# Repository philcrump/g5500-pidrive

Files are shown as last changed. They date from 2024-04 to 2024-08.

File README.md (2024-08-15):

# G-5500 PiDrive

***This project is a work in progress, very little testing has so far been done, I supply no guarantee that the basic concepts work***

Controlling an AC-type Yaesu G-5500 Az+El Rotator with PWM from a Raspberry Pi, allowing a portable and compact drive unit running off a 12V battery with no mains inverters.

Choices have been made to use high-end voltage-isolated parts to allow easy co-existence with multiple power domains, as several RF receivers will also be connected to the Raspberry Pi.

## Physical Form Factor

PWM board intends to mount on the _back_ of an RPI DIN Plate, facing the Host Raspberry Pi on another DIN plate, connected by Adafruit GPIO Ribbon Cable.
* https://thepihut.com/products/dinrplate-2-raspberry-pi-din-rail-mount

PCB Render:

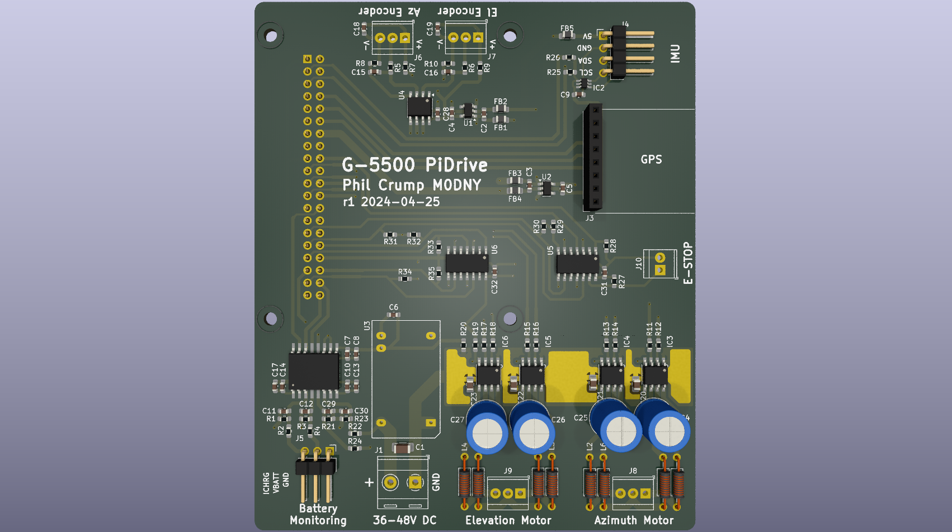
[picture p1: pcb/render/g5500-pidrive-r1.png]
PCB CAD Render


### Supply Voltage

36-48V Input, Tracpower Isolated TEL 12-4811WI DC-DC converts down to 5.1V @ 2.4A for the Raspberry Pi.

MAX22530 12-bit Isolated ADC cam measure the input voltage, and also exposes a connector to measure 12V battery voltage, and an optional extra channel (charge current?)

## G-5500 Control

### Motor Drive

Yaesu mains control box produces 80V pk-pk AC. Initially I plan to use a cheap 12V -> 36V DC-DC step-up to allow output of 72V pk-pk AC. The design allows for increasing to 48V motor bus voltage.

DRV8251A 4.1A Motor drivers used to achieve 50Hz AC PWM over the relevant winding for each direction. Initial experiments with variable-frequency were not very successful, but there may be +/-10% to play with for accel/decel softening.

E-STOP implemented with hardware logic (high-speed CMOS) holds motors in 'Brake' regardless of software - if switch contact is opened.

Footprints have been included to allow the use of RF chokes on the PWM outputs if RFI problems are encountered.

### Potentiometer sensing

MCP3202 12-bit ADC measures the wiper voltage on each of the Az+El Potentiometers to sense position. Careful decoupling of the supply voltage and filtering of the wiper voltage is implemented to achieve a low-noise result.

## Position / Alignment Sensors

* Uputronics Ublox GPS Breakout as daughterboard for Time + Position https://store.uputronics.com/index.php?route=product/product&path=64&product_id=84
* * Connection for NTPD Timing setup with PPS https://austinsnerdythings.com/2021/04/19/microsecond-accurate-ntp-with-a-raspberry-pi-and-pps-gps/

* BNO055 DOF IMU Fusion for magnetic-north calibration https://thepihut.com/products/adafruit-9-dof-absolute-orientation-imu-fusion-breakout-bno055
* * Mounted at end of aluminium boom
* * Active I2C LTC4311 Terminator to extend the I2C far enough down the boom (screened cable will be used.)

## Software

Motor drive using pigpio's excellent ability to run hardware-timed PWM on every GPIO. https://abyz.me.uk/rpi/pigpio/index.html

## Tests

* Body diode clamping of high-z driver on other pole is enough to prevent motion of AC motor.
* Heatsinking of existing drivers is very inadequate. (Blown EL_B1/EL_B2 )
* * Added DIY copper tab heatsinks to both side of PCB
* 22R resistor between 48V & 5V ground domains had approx 1V across it (~50mA)
* * Removed & shorted out.

* Pi Running: 0.07A @ 48V
* 1x Motor drive: 0.67A @ 48V

For attachment to mast pole: https://www.ebay.co.uk/itm/265428394116

ebay wire is 16awg 1.5mm^2

12-48V: https://uk.rs-online.com/web/p/dc-dc-converters/1757784

M3.5 ring terminals for meanwell 12v mains PSU   https://uk.rs-online.com/web/p/ring-terminals/0534222

## Authors

* Phil Crump M0DNY <phil@philcrump.co.uk>

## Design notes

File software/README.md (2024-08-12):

Raspberry Pi OS Bookworm

## C

gcc -Wall -pthread -o pwmtest main.c -lpigpio

# IMU Setup

Raspi-config -> Interface Options ->**Disable** I2C Kernel module.

```bash
sudo bash -c "echo 'dtoverlay=i2c-gpio,i2c_gpio_sda=2,i2c_gpio_scl=3,bus=3' >> /boot/firmware/config.txt"
```
# GPS Setup

Raspi-config -> Interface Options -> Disable Serial Port Console, Enable Serial Port.

( /dev/ttyS0 )

```bash
sudo apt install gpsd pps-tools chrony libgps-dev

sudo bash -c "echo 'dtoverlay=pps-gpio,gpiopin=18' >> /boot/firmware/config.txt"
sudo bash -c "echo 'enable_uart=1' >> /boot/firmware/config.txt"
sudo bash -c "echo 'init_uart_baud=9600' >> /boot/firmware/config.txt"
sudo bash -c "echo 'pps-gpio' >> /etc/modules"
```
Reboot.

Check PPS: `sudo ppstest /dev/pps0`

`sudo nano /etc/default/gpsd`
```
START_DAEMON="true"
USBAUTO="false"
DEVICES="/dev/ttyS0 /dev/pps0"
GPSD_OPTIONS="-n"
```

`sudo systemctl start gpsd`

sudo nano /etc/chrony/chrony.conf

Under pool entry, add:
```
refclock SHM 0 refid NMEA offset 0.000 precision 1e-3 poll 3 noselect
refclock PPS /dev/pps0 refid PPS lock NMEA poll 3
```
sudo systemctl restart chrony

watch -n 1 chronyc sources

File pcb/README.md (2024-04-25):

1x LTC4311 SOT-323-5

4x DRV8251A

4x 8X11.5mm LS:5mm   82uF 63V     667-EEU-FR1J820B 

Ferrites:
0805 40mohm 3A     652-MH2029-800Y

1x 579-MCP3202BISN MCP3202 B-grade SOIC

1x MAX22530AWE+ Isolated ADC

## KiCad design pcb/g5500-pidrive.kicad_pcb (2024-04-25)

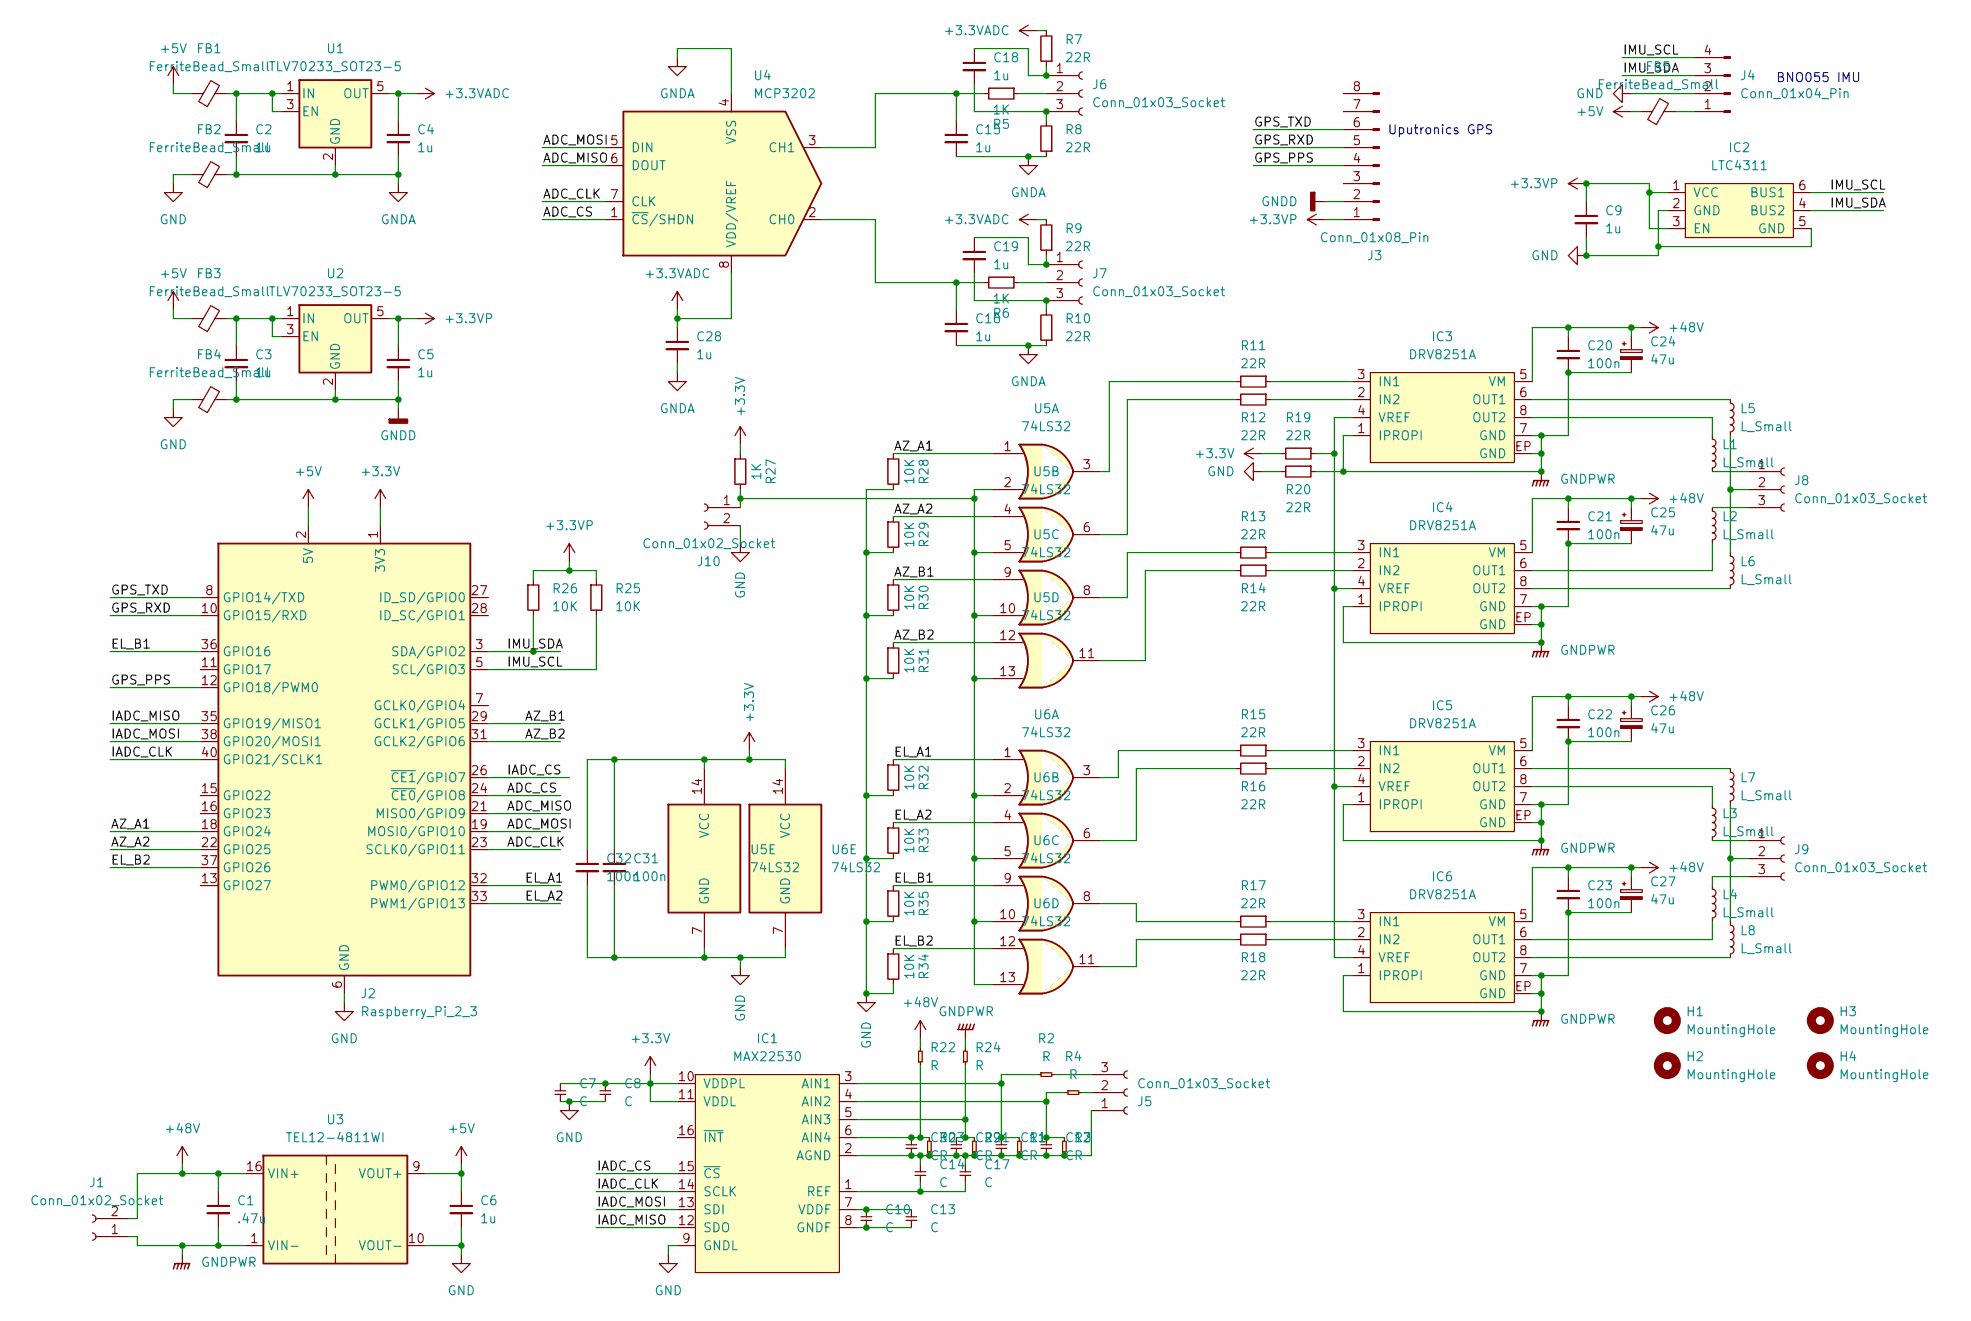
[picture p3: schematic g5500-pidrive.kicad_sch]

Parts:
C1: .47u; C_1206_3216Metric_Pad1.33x1.80mm_HandSolder
C2, C3, C4, C5, C6, C9, C15, C16, C18, C19, C28: 1u; C_0603_1608Metric_Pad1.08x0.95mm_HandSolder
C7, C8, C10, C11, C12, C13, C14, C17, C29, C30: C; C_0603_1608Metric_Pad1.08x0.95mm_HandSolder
C20, C21, C22, C23: 100n; C_0805_2012Metric_Pad1.18x1.45mm_HandSolder
C24, C25, C26, C27: 47u; C_Radial_D8.0mm_H11.5mm_P3.50mm
C31, C32: 100n; C_0603_1608Metric_Pad1.08x0.95mm_HandSolder
FB1, FB2, FB3, FB4, FB5: FerriteBead_Small; L_0805_2012Metric_Pad1.05x1.20mm_HandSolder
H1, H2, H3, H4: MountingHole; MountingHole_2.7mm_M2.5
IC1: MAX22530; SOIC-16-W; Mouser 700-MAX22530AWE+
IC2: LTC4311; SC-70-6; Mouser 584-C4311CSC6TRMPBF
IC3, IC4, IC5, IC6: DRV8251A; SOIC-8-EP; Mouser 595-DRV8251ADDAR
J1: Conn_01x02_Socket; TerminalBlock_RND_205-00287_1x02_P5.08mm_Horizontal
J2: Raspberry_Pi_2_3; PinSocket_2x20_P2.54mm_Vertical
J3: Conn_01x08_Pin; PinSocket_1x08_P2.54mm_Vertical
J4: Conn_01x04_Pin; PinHeader_1x04_P2.54mm_Horizontal
J5: Conn_01x03_Socket; PinHeader_1x03_P2.54mm_Horizontal
J6, J7, J8, J9: Conn_01x03_Socket; TerminalBlock_TE_282834-3_1x03_P2.54mm_Horizontal
J10: Conn_01x02_Socket; TerminalBlock_TE_282834-2_1x02_P2.54mm_Horizontal
L1, L2, L3, L4, L5, L6, L7, L8: L_Small; L_Axial_L5.3mm_D2.2mm_P10.16mm_Horizontal_Vishay_IM-1
R1, R2, R3, R4, R21, R22, R23, R24: R; R_0603_1608Metric_Pad0.98x0.95mm_HandSolder
R5, R6, R27: 1K; R_0603_1608Metric_Pad0.98x0.95mm_HandSolder
R7, R8, R9, R10, R11, R12, R13, R14, R15, R16, R17, R18, R19, R20: 22R; R_0603_1608Metric_Pad0.98x0.95mm_HandSolder
R25, R26, R28, R29, R30, R31, R32, R33, R34, R35: 10K; R_0603_1608Metric_Pad0.98x0.95mm_HandSolder
U1, U2: TLV70233_SOT23-5; SOT-23-5
U3: TEL12-4811WI; Converter_DCDC_TRACO_TEL12-xxxx_THT
U4: MCP3202; SOIC-8_3.9x4.9mm_P1.27mm
U5, U6: 74LS32; SOIC-14

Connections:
+3.3V: C7.2, C8.2, C31.1, C32.1, IC1.10 (VDDPL), IC1.11 (VDDL), J2.1 (3V3), J2.17 (3V3), R19.2, R27.1, U5.14 (VCC), U6.14 (VCC)
+3.3VADC: C4.1, C28.1, R7.2, R9.2, U1.5 (OUT), U4.8 (VDD/VREF)
+3.3VP: C5.1, C9.1, IC2.1 (VCC), IC2.3 (EN), J3.1, R25.1, R26.1, U2.5 (OUT)
+5V: C6.1, FB1.1, FB3.1, FB5.1, J2.2 (5V), J2.4 (5V), U3.9 (VOUT+)
+48V: C1.1, C20.1, C21.1, C22.1, C23.1, C24.1, C25.1, C26.1, C27.1, IC3.5 (VM), IC4.5 (VM), IC5.5 (VM), IC6.5 (VM), J1.2, R22.2, U3.16 (VIN+)
/ADC_CLK: J2.23 (SCLK0/GPIO11), U4.7 (CLK)
/ADC_CS: J2.24 (~CE0/GPIO8), U4.1 (~CS/SHDN)
/ADC_MISO: J2.21 (MISO0/GPIO9), U4.6 (DOUT)
/ADC_MOSI: J2.19 (MOSI0/GPIO10), U4.5 (DIN)
/AZ_A1: J2.18 (GPIO24), R28.1, U5.1
/AZ_A2: J2.22 (GPIO25), R29.1, U5.4
/AZ_B1: J2.29 (GCLK1/GPIO5), R30.1, U5.9
/AZ_B2: J2.31 (GCLK2/GPIO6), R31.1, U5.12
/EL_A1: J2.32 (PWM0/GPIO12), R32.1, U6.1
/EL_A2: J2.33 (PWM1/GPIO13), R33.1, U6.4
/EL_B1: J2.36 (GPIO16), R35.1, U6.9
/EL_B2: J2.37 (GPIO26), R34.1, U6.12
/GPS_PPS: J2.12 (GPIO18/PWM0), J3.4
/GPS_RXD: J2.10 (GPIO15/RXD), J3.5
/GPS_TXD: J2.8 (GPIO14/TXD), J3.6
/IADC_CLK: IC1.14 (SCLK), J2.40 (GPIO21/SCLK1)
/IADC_CS: IC1.15 (~CS), J2.26 (~CE1/GPIO7)
/IADC_MISO: IC1.12 (SDO), J2.35 (GPIO19/MISO1)
/IADC_MOSI: IC1.13 (SDI), J2.38 (GPIO20/MOSI1)
/IMU_SCL: IC2.6 (BUS1), J2.5 (SCL/GPIO3), J4.4, R25.2
/IMU_SDA: IC2.4 (BUS2), J2.3 (SDA/GPIO2), J4.3, R26.2
GND: C6.2, C7.1, C8.1, C9.2, C31.2, C32.2, FB2.1, FB4.1, IC1.9 (GNDL), IC2.2 (GND), IC2.5 (GND), J2.6 (GND), J2.9 (GND), J2.14 (GND), J2.20 (GND), J2.25 (GND), J2.30 (GND), J2.34 (GND), J2.39 (GND), J4.2, J10.2, R20.2, R28.2, R29.2, R30.2, R31.2, R32.2, R33.2, R34.2, R35.2, U3.10 (VOUT-), U5.7 (GND), U6.7 (GND)
GNDA: C2.2, C4.2, C15.2, C16.2, C28.2, FB2.2, R8.1, R10.1, U1.2 (GND), U4.4 (VSS)
GNDD: C3.2, C5.2, FB4.2, J3.2, U2.2 (GND)
GNDPWR: C1.2, C20.2, C21.2, C22.2, C23.2, C24.2, C25.2, C26.2, C27.2, IC3.1 (IPROPI), IC3.7 (GND), IC3.EP (GND), IC4.1 (IPROPI), IC4.7 (GND), IC4.EP (GND), IC5.1 (IPROPI), IC5.7 (GND), IC5.EP (GND), IC6.1 (IPROPI), IC6.7 (GND), IC6.EP (GND), J1.1, R20.1, R24.2, U3.1 (VIN-)
unnamed: C11.1, C12.1, C14.1, C17.1, C29.1, C30.1, IC1.2 (AGND), J5.1, R1.1, R3.1, R21.1, R23.1
unnamed: C11.2, IC1.3 (AIN1), R1.2, R2.1
unnamed: C12.2, IC1.4 (AIN2), R3.2, R4.1
unnamed: C29.2, IC1.5 (AIN3), R21.2, R24.1
unnamed: C30.2, IC1.6 (AIN4), R22.1, R23.2
unnamed: C10.1, C13.1, IC1.8 (GNDF)
unnamed: C14.2, C17.2, IC1.1 (REF)
unnamed: C10.2, C13.2, IC1.7 (VDDF)
unnamed: IC3.3 (IN1), R11.1
unnamed: IC3.2 (IN2), R12.1
unnamed: IC3.6 (OUT1), L5.1
unnamed: IC3.8 (OUT2), L1.1
unnamed: IC3.4 (VREF), IC4.4 (VREF), IC5.4 (VREF), IC6.4 (VREF), R19.1
unnamed: IC4.3 (IN1), R13.1
unnamed: IC4.2 (IN2), R14.1
unnamed: IC4.6 (OUT1), L2.2
unnamed: IC4.8 (OUT2), L6.2
unnamed: IC5.3 (IN1), R15.1
unnamed: IC5.2 (IN2), R16.1
unnamed: IC5.6 (OUT1), L7.1
unnamed: IC5.8 (OUT2), L3.1
unnamed: IC6.3 (IN1), R17.1
unnamed: IC6.2 (IN2), R18.1
unnamed: IC6.6 (OUT1), L4.2
unnamed: IC6.8 (OUT2), L8.2
unnamed: FB5.2, J4.1
unnamed: J5.2, R4.2
unnamed: J5.3, R2.2
unnamed: C18.1, J6.1, R7.1
unnamed: J6.2, R5.1
unnamed: C18.2, J6.3, R8.2
unnamed: C19.1, J7.1, R9.1
unnamed: J7.2, R6.1
unnamed: C19.2, J7.3, R10.2
unnamed: J8.1, L1.2
unnamed: J8.2, L5.2, L6.1
unnamed: J8.3, L2.1
unnamed: J9.1, L3.2
unnamed: J9.2, L7.2, L8.1
unnamed: J9.3, L4.1
unnamed: J10.1, R27.2, U5.2, U5.5, U5.10, U5.13, U6.2, U6.5, U6.10, U6.13
unnamed: R11.2, U5.3
unnamed: R12.2, U5.6
unnamed: R13.2, U5.8
unnamed: R14.2, U5.11
unnamed: R15.2, U6.3
unnamed: R16.2, U6.6
unnamed: R17.2, U6.8
unnamed: R18.2, U6.11
unnamed: C2.1, FB1.2, U1.1 (IN), U1.3 (EN)
unnamed: C3.1, FB3.2, U2.1 (IN), U2.3 (EN)
unnamed: C16.1, R6.2, U4.2 (CH0)
unnamed: C15.1, R5.2, U4.3 (CH1)

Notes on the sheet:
Uputronics GPS
BNO055 IMU

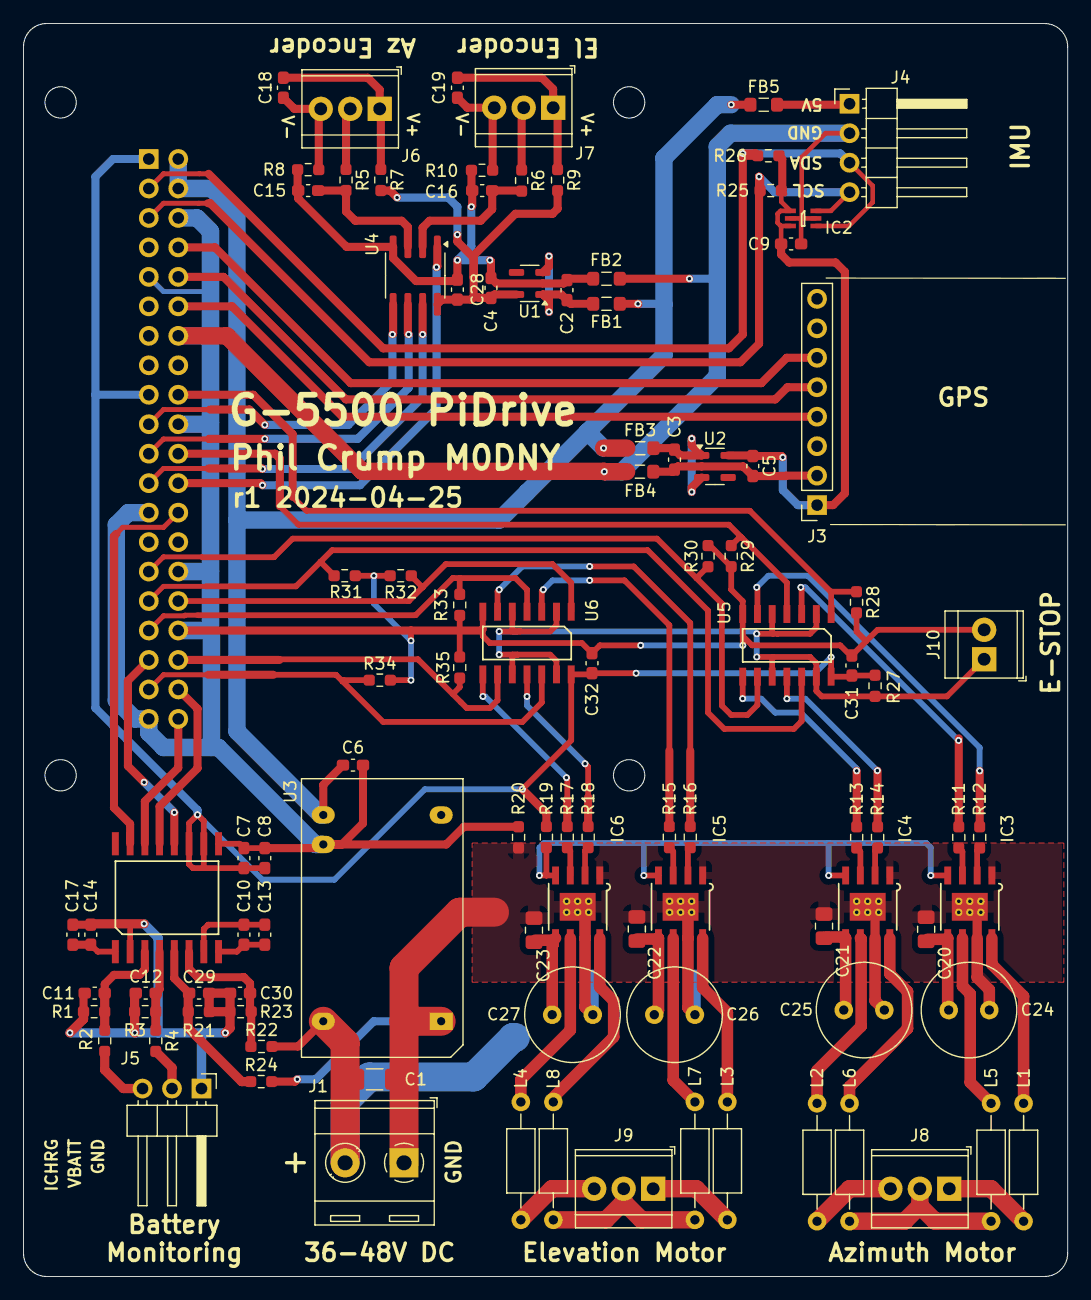
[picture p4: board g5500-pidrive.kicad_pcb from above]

Board: 2 copper layers, 90.0 x 108.0 mm, 106 parts (1 on the bottom side), 83 nets.

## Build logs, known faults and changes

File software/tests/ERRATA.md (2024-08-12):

GPS TX/RX reversed.

MAX ADC SPI CS needs to be connected to GPIO 17.

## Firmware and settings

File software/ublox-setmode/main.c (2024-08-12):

#include <stdio.h>
#include <string.h>
#include <termios.h>
#include <unistd.h>
#include <sys/types.h>
#include <sys/stat.h>
#include <stdint.h>
#include <stdbool.h>
#include <fcntl.h>

bool verbose = false;

const int32_t gnss_aid_position_latitude    = (51.64 / 1e-7); // mid-south-England
const int32_t gnss_aid_position_longitude   = (-1.48 / 1e-7);
const int32_t gnss_aid_position_altitude    =    (10 / 1e-2); // 10m
const int32_t gnss_aid_position_stddev      =   (199 / 1e-5); // 199km

uint8_t gnss_hard_reset[] =
    {   0xB5, 0x62,
        0x06, 0x04, // UBX-CFG-RST
        0x04, 0x00, // Length
        0xff, 0xff, // navBbrMask (0 = hot, 1 = warm, ffff = cold)
        0x04, // resetMode (0 = hardware, 1 = software, 2 = gnss, 4 = shutdown then hardware)
        0x00, // Reserved
        0x00, 0x00 // Checksum
    };

uint8_t gnss_aid_position[] =
    {   0xB5, 0x62,
        0x13, 0x40, // UBX-MGA-INI
        0x14, 0x00, // Length
        0x01, // Type: UBX-MGA-INI-POS_LLH
        0x00, // Version: 0
        0x00, 0x00, // Reserved
        0x00, 0x00, 0x00, 0x00, // Latitude 1e-7
        0x00, 0x00, 0x00, 0x00, // Longitude 1e-7
        0x00, 0x00, 0x00, 0x00, // Altitude cm
        0x00, 0x00, 0x00, 0x00, // Std Dev cm
        0x00, 0x00 // Checksum
    };

uint8_t set_navmodel_stationary[] =
    {   0xB5, 0x62,
        0x06, 0x24, // UBX-CFG-NAV5
        0x24, 0x00, // Length 
        0xFF, 0xFF, // Bitmask
        0x02, // Model (Stationary = 0x02, airborne = 0x06)
        0x03, // Fix Type (Auto 2D/3D)
        0x00, 0x00, 0x00, 0x00, // 2D Altitude Value
        0x10, 0x27, 0x00, 0x00, // 2D Altitude Variance
        0x05, // Minimum GNSS Satellite Elevation
        0x00, // Reserved
        0xFA, 0x00, // Position DOP Mask
        0xFA, 0x00, // Time DOP Mask
        0x64, 0x00, // Position Accuracy Mask
        0x2C, 0x01, // Time Accuracy Mask
        0x00, // Static hold threshold
        0x00, // DGNSS Timeout
        0x00, // Min Satellites for Fix
        0x00, // Min C/N0 Threshold for Satellites
        0x10, 0x27, // Reserved
        0x00, 0x00, // Static Hold Distance Threshold
        0x00, // UTC Standard (Automatic)
        0x00, 0x00, 0x00, 0x00, 0x00,
        0x00, 0x00 // Checksum
    };

uint8_t set_sbas_egnos[] =
    {   0xB5, 0x62,
        0x06, 0x16, // UBX-CFG-SBAS
        0x08, 0x00, // Length
        0x01, // Mode (enabled)
        0x07, // Usage (range, corrections, integrity)
        0x03, // SBAS Channels (3, field obselete)
        0x00, 0x51, 0x08, 0x00, 0x00, // PRN Bitmask (EGNOS-only)
        0x00, 0x00 // Checksum
    };

void usage( void )
{
    printf("Usage: ubloxSetMode -d <device>\n");  
}
 
unsigned char ReadBByteFromSerial(int fd, int *k)
{
    unsigned char tmp;
   
    (*k)++;
     
    if (read(fd, &tmp, 1) > 0)
    {
        // if (tmp & 0x80)
        // {
            // printf("<%2x> ", tmp);
        // }
        // else
        // {
            // printf("%c", tmp);
        // }
    }
   
    return tmp;
}

void calcChecksum(uint8_t *command, int32_t command_length)
{
    uint8_t ck_a = 0, ck_b = 0;
    for(int32_t i = 2; i < (command_length-2); i++)
    {
        ck_a += command[i];
        ck_b += ck_a;
    }
    command[command_length-2] = ck_a;
    command[command_length-1] = ck_b;

    //printf("ck: 0x%02x, 0x%02x\n", ck_a, ck_b);
}

bool setMode(int fd, uint8_t *command, int32_t command_length)
{
    int Retries, k;
    bool result;

    Retries = 0;
    k = 0;
    result = false;
   
    while ((Retries < 5) && !result)
    {
        calcChecksum(command, command_length);

        if(verbose) printf(">> Sending Command (Attempt %d of 5) >>\n", (Retries+1));
        if(write(fd, command, command_length) != command_length)
        {
            Retries++;
            continue;
        }
       
        Retries++;
        k = 0;
       
        if(verbose) printf("<< Receiving ACK <<\n");
        while ((k < 1000) && !result)
        {
            /* Check for ACK */
            if (ReadBByteFromSerial(fd, &k) == 0xb5)
            {
                if (ReadBByteFromSerial(fd, &k) == 0x62)
                {
                    if (ReadBByteFromSerial(fd, &k) == 0x05)
                    {
                        if (ReadBByteFromSerial(fd, &k) == 0x01)
                        {
                            ReadBByteFromSerial(fd, &k);
                            ReadBByteFromSerial(fd, &k);

                            /* Check ACK is for correct message ID */
                            if (ReadBByteFromSerial(fd, &k) == command[2])
                            {
                                if (ReadBByteFromSerial(fd, &k) == command[3])
                                {
                                    if(verbose) printf("|| Received ACK OK!\n");
                                    result = true;
                                }
                            }
                        }
                    }
                }
            }
        }
    }

    return result;
}
 
int main(int argc, char *argv[])
{   
    bool result;
    int fd;
    int option = 0;
    char devName[50];
    struct termios options;
   
    memset(devName, 0, sizeof(devName));
    while((option = getopt( argc, argv, "vd:")) != -1)
    {
        switch(option)
        {
            case 'd':
                printf("Configuring serial device: %s\n", optarg);
                strncpy(devName, optarg, sizeof(devName)-1);                
                break;
            case 'v':
                printf(" * Verbose Mode Enabled\n");
                verbose = true;
                break;
            default:
                usage();
                return 0;
        }        
    }
 
    if(devName[0] == 0)
    {
        usage();
        return 1;
    }
       
    /* Open Serial Port */
    fd = open(devName, O_RDWR);
    if(fd < 0)
    {
        printf("Error: Cannot open serial device '%s'\n", devName);
        return 1;
    }
     
    /* Configure Serial Port */
    tcgetattr(fd, &options);
 
    options.c_lflag &= ~ECHO;
    options.c_cc[VMIN]  = 0;
    options.c_cc[VTIME] = 10;
 
    cfsetispeed(&options, B9600);
    cfsetospeed(&options, B9600);
    options.c_cflag &= ~CSTOPB;
    options.c_cflag &= ~CSIZE;
    options.c_cflag |= CS8;
    options.c_oflag &= ~ONLCR;
    options.c_oflag &= ~OPOST;
    options.c_iflag &= ~IXON;
    options.c_iflag &= ~IXOFF;
 
    tcsetattr(fd, TCSANOW, &options);

    memcpy(&gnss_aid_position[8], &gnss_aid_position_latitude, sizeof(int32_t));
    memcpy(&gnss_aid_position[12], &gnss_aid_position_longitude, sizeof(int32_t));
    memcpy(&gnss_aid_position[16], &gnss_aid_position_altitude, sizeof(int32_t));
    memcpy(&gnss_aid_position[20], &gnss_aid_position_stddev, sizeof(int32_t));
    calcChecksum(gnss_aid_position, sizeof(gnss_aid_position));

    printf("Configuring Position Aid..\n");
    result = setMode(fd, gnss_aid_position, sizeof(gnss_aid_position));
    if(!result)
    {
        printf("** FAILED to configure Position Aid **\n");
        close(fd);
        return 1;
    }

    printf("Configuring Navigation Model..\n");
    result = setMode(fd, set_navmodel_stationary, sizeof(set_navmodel_stationary));
    if(!result)
    {
        printf("** FAILED to configure Navigation Model **\n");
        close(fd);
        return 1;
    }
 
    printf("Configuring SBAS Mode for EGNOS..\n");
    result = setMode(fd, set_sbas_egnos, sizeof(set_sbas_egnos));
    if(!result)
    {
        printf("** FAILED to configure SBAS Mode **\n");
        close(fd);
        return 1;
    }

    close(fd);

    printf("Device Configuration Successful\n");
   
    return 0;
}

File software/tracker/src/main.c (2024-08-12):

#include <stdio.h>
#include <unistd.h>
#include <stdlib.h>
#include <errno.h>
#include <pthread.h>
#include <signal.h>
#include <math.h>

#include <pigpio.h>

#include "main.h"
#include "adc_encoder.h"
#include "adc_supplies.h"
#include "imu.h"
#include "gpsd.h"
#include "motordrive.h"


app_state_t app_state = {
    .demand_valid = false,
    .current_valid = false,
    .voltages_valid = false,
    .gpsd_valid = false,
    .imu_valid = false,
    .compass_valid = false,
    .app_exit = false
};

void sigint_handler(int sig) 
{
    (void)sig;
    printf("\nCTRL-C detected...\n");
    app_state.app_exit = true;
}

int main(int argc, char **argv)
{
    (void)argc;
    (void)argv;

    /* Override pigpio handler */
    signal(SIGINT, sigint_handler);
    signal(SIGTERM, sigint_handler);

    if(gpioInitialise() < 0)
    {
        fprintf(stderr, "Error: gpio failed to initialise\n");
        return 1;
    }
    gpioWaveClear();

    //printf("pigpio version %d.\n", gpioVersion());
    //printf("Hardware revision %d.\n", gpioHardwareRevision());

    /* Override pigpio handler */
    signal(SIGINT, sigint_handler);
    signal(SIGTERM, sigint_handler);

    // threads
    pthread_t adcs_pthread;
    pthread_t imu_obj;
    pthread_t gpsd_obj;
    pthread_t motordrive_obj;

    // ADC Encoders Thread
    if(0 != pthread_create(&adcs_pthread, NULL, adc_loop, (void *)&app_state))
    {
        fprintf(stderr, "Error creating %s pthread\n", "adc_encoder");
        return 1;
    }
    pthread_setname_np(adcs_pthread, "adcs");

    // IMU Thread
    if(0 != pthread_create(&imu_obj, NULL, imu_thread, (void *)&app_state))
    {
        fprintf(stderr, "Error creating %s pthread\n", "imu");
        return 1;
    }
    pthread_setname_np(imu_obj, "imu");

    // GPSD Thread
    if(0 != pthread_create(&gpsd_obj, NULL, gpsd_thread, (void *)&app_state))
    {
        fprintf(stderr, "Error creating %s pthread\n", "gpsd");
        return 1;
    }
    pthread_setname_np(gpsd_obj, "gpsd");

    if(0 != pthread_create(&motordrive_obj, NULL, motordrive_thread, (void *)&app_state))
    {
        fprintf(stderr, "Error creating %s pthread\n", "motordrive");
        return 1;
    }
    pthread_setname_np(motordrive_obj, "motordrive");

    app_state.demand_az_deg = 250.0;
    app_state.demand_el_deg = 90.0;
    app_state.demand_valid = true;


    while(!(app_state.app_exit))
    {
        if(app_state.voltages_valid)
        {
            printf("PoE Voltage: %.2fV, Battery Voltage: %.2fV\n", app_state.poe_voltage, app_state.batt_voltage);
        }
        if(app_state.gpsd_valid)
        {
            if(app_state.gpsd_fixmode >= 2)
            {
                printf("GPS Fix: %dD (%02d), Lat: %.6f, Lon: %.6f\n", app_state.gpsd_fixmode, app_state.gpsd_sats, app_state.gpsd_latitude,  app_state.gpsd_longitude);
            }
            else
            {
                printf("GPS Fix: %dD (%02d)\n", app_state.gpsd_fixmode, app_state.gpsd_sats);
            }
        }
        if(app_state.current_valid)
        {
            printf("Current: Az: %.01f, El: %0.1f\n", app_state.current_az_deg, app_state.current_el_deg);
        }
        if(app_state.imu_valid)
        {
            printf("Heading: %+03.1f (%01x), Roll: %+03.1f, Pitch: %+03.1f\n", app_state.imu_heading, app_state.imu_heading_calstatus, app_state.imu_roll, app_state.imu_pitch);
        }

        usleep(500*1000); // 20 Hz
    }

    printf("Terminating threads..\n");

    pthread_join(adcs_pthread, NULL);
    pthread_join(gpsd_obj, NULL);
    pthread_join(motordrive_obj, NULL);

    printf("Terminating GPIO\n");

    gpioTerminate();

    return 0;
}

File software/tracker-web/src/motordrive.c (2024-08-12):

#include <stdio.h>
#include <stdlib.h>
#include <unistd.h>
#include <stdbool.h>
#include <signal.h>

#include <math.h>
#include <pigpio.h>

#include "main.h"
#include "util/timing.h"

#define AZ_HYSTERESIS   (1.5)
#define EL_HYSTERESIS   (1.0)

#define AZ_RELAY_PAUSE_MS   (200)
#define EL_RELAY_PAUSE_MS   (200)

#define WAVEFORM_POINTS     (1000)
#define WAVEFORM_PERIOD_US  (40)

#define AZ_CW_P     (24)
#define AZ_CW_N     (25)

#define AZ_CCW_P    (5) // unused (popped)
#define AZ_CCW_N    (6) // unused (popped)

#define EL_CW_P     (12)
#define EL_CW_N     (13)

#define EL_CCW_P    (16) //unused
#define EL_CCW_N    (26) // unused

#define AZ_SWITCH_GPIO  (27)
#define EL_SWITCH_GPIO  (22)

void *loop_motordrive(void *arg)
{
  app_state_t *app_state = (app_state_t *)arg;

  float phase_angle, sine_amplitude, duty_cycle;

  gpioPulse_t *az_wf = (gpioPulse_t *)malloc(WAVEFORM_POINTS * sizeof(gpioPulse_t));
  if(az_wf == NULL)
  {
    fprintf(stderr, "Motordrive: Error allocating local memory for waveform\n");
    return NULL;
  }

  gpioPulse_t *el_wf = (gpioPulse_t *)malloc(WAVEFORM_POINTS * sizeof(gpioPulse_t));
  if(el_wf == NULL)
  {
    fprintf(stderr, "Motordrive: Error allocating local memory for waveform\n");
    free(az_wf);
    return NULL;
  }

  gpioPulse_t *azel_wf = (gpioPulse_t *)malloc(WAVEFORM_POINTS * sizeof(gpioPulse_t));
  if(azel_wf == NULL)
  {
    fprintf(stderr, "Motordrive: Error allocating local memory for waveform\n");
    free(az_wf);
    free(el_wf);
    return NULL;
  }

  int gpio_az, gpio_el;

  for(int i = 0; i < WAVEFORM_POINTS; i++)
  {
    phase_angle = i * ((2*M_PI) / (float)WAVEFORM_POINTS);
    sine_amplitude = sin(phase_angle);

    if(sine_amplitude >= 0)
    {
      /* Positive half of wave */
      gpio_az = 1 << (AZ_CW_P);
      gpio_el = 1 << (EL_CW_P);
    }
    else
    {
      gpio_az = 1 << (AZ_CW_N);
      gpio_el = 1 << (EL_CW_N);
    }

    duty_cycle = fabs(sine_amplitude) * 0.9;

    if((i & 0x01) == 0x00)
    {
      az_wf[i].gpioOn = gpio_az;
      el_wf[i].gpioOn = gpio_el;
      azel_wf[i].gpioOn = (gpio_az | gpio_el);

      az_wf[i].gpioOff = 0;
      el_wf[i].gpioOff = 0;
      azel_wf[i].gpioOff = 0;

      az_wf[i].usDelay = (int)(round(duty_cycle * WAVEFORM_PERIOD_US));
      el_wf[i].usDelay = (int)(round(duty_cycle * WAVEFORM_PERIOD_US));
      azel_wf[i].usDelay = (int)(round(duty_cycle * WAVEFORM_PERIOD_US));
    }
    else
    {

      az_wf[i].gpioOn = 0;
      el_wf[i].gpioOn = 0;
      azel_wf[i].gpioOn = 0;

      az_wf[i].gpioOff = gpio_az;
      el_wf[i].gpioOff = gpio_el;
      azel_wf[i].gpioOff = (gpio_az | gpio_el);

      az_wf[i].usDelay = WAVEFORM_PERIOD_US - (int)(round(duty_cycle * WAVEFORM_PERIOD_US));
      el_wf[i].usDelay = WAVEFORM_PERIOD_US - (int)(round(duty_cycle * WAVEFORM_PERIOD_US));
      azel_wf[i].usDelay = WAVEFORM_PERIOD_US - (int)(round(duty_cycle * WAVEFORM_PERIOD_US));
    }
  }

  int e, az_wave, el_wave, azel_wave;

  e = gpioWaveAddGeneric(WAVEFORM_POINTS, az_wf);
  if(e < 0)
  {
    fprintf(stderr, "Failed to add az_wf Waveform to gpio: %d\n", e);
  }
  az_wave = gpioWaveCreate();
  if(az_wave < 0)
  {
    fprintf(stderr, "Failed to create az_wave Waveform: %d\n", e);
  }

  e = gpioWaveAddGeneric(WAVEFORM_POINTS, el_wf);
  if(e < 0)
  {
    fprintf(stderr, "Failed to add el_wf Waveform to gpio: %d\n", e);
  }
  el_wave = gpioWaveCreate();
  if(el_wave < 0)
  {
    fprintf(stderr, "Failed to create el_wave Waveform: %d\n", e);
  }

  e = gpioWaveAddGeneric(WAVEFORM_POINTS, azel_wf);
  if(e < 0)
  {
    fprintf(stderr, "Failed to add azel_wf Waveform to gpio: %d\n", e);
  }
  azel_wave = gpioWaveCreate();
  if(azel_wave < 0)
  {
    fprintf(stderr, "Failed to create azel_wave Waveform: %d\n", e);
  }

  /* Set up outputs */

  gpioSetMode(AZ_CW_P, PI_OUTPUT);
  gpioSetMode(AZ_CW_N, PI_OUTPUT);

  gpioSetMode(AZ_CCW_P, PI_OUTPUT);
  gpioSetMode(AZ_CCW_N, PI_OUTPUT);

  gpioSetMode(EL_CW_P, PI_OUTPUT);
  gpioSetMode(EL_CW_N, PI_OUTPUT);

  gpioSetMode(EL_CCW_P, PI_OUTPUT);
  gpioSetMode(EL_CCW_N, PI_OUTPUT);

  gpioWrite_Bits_0_31_Clear(
    1 << (EL_CW_P) | 1 << (EL_CW_N) | 1 << (EL_CCW_P) | 1 << (EL_CCW_N)
    | 1 << (AZ_CW_P) | 1 << (AZ_CW_N) | 1 << (AZ_CCW_P) | 1 << (AZ_CCW_N)
  );

  /* Direction Relays */
  gpioSetMode(AZ_SWITCH_GPIO, PI_OUTPUT);
  gpioSetMode(EL_SWITCH_GPIO, PI_OUTPUT);

  gpioWrite(AZ_SWITCH_GPIO, 0);
  gpioWrite(EL_SWITCH_GPIO, 0);

  enum WAVE_STATE {
    WAVE_OFF,
    WAVE_AZ,
    WAVE_EL,
    WAVE_AZEL
  };

  int32_t pwm_state = WAVE_OFF;

  int32_t az_relay_state = 0;
  int32_t el_relay_state = 0;

  uint64_t az_relay_lastswitch = timestamp_ms();
  uint64_t el_relay_lastswitch = timestamp_ms();

  /* Run waves */
  while(!(app_state->app_exit))
  {
    if(app_state->demand_valid
      && app_state->encoder_valid
    )
    {
      app_state->error_az_deg = app_state->encoder_az_deg - app_state->demand_az_deg;
      app_state->error_el_deg = app_state->encoder_el_deg - app_state->demand_el_deg;
      app_state->error_lastupdated_ms = timestamp_ms();
      app_state->error_valid = true;

      // Check Azimuth
      if(app_state->error_az_deg > AZ_HYSTERESIS
        && (az_relay_lastswitch + AZ_RELAY_PAUSE_MS) < timestamp_ms())
      {
        if(az_relay_state == 0)
        {
          gpioWrite(AZ_SWITCH_GPIO, 1);
          az_relay_state = 1;

          az_relay_lastswitch = timestamp_ms();
        }
        else
        {
          if(pwm_state != WAVE_AZ && pwm_state != WAVE_AZEL)
          {
            if(pwm_state == WAVE_EL)
            {
              /* Stop the El-only wave */
              gpioWaveTxStop();
              gpioWrite_Bits_0_31_Clear(
                1 << (EL_CW_P) | 1 << (EL_CW_N) | 1 << (EL_CCW_P) | 1 << (EL_CCW_N)
                | 1 << (AZ_CW_P) | 1 << (AZ_CW_N) | 1 << (AZ_CCW_P) | 1 << (AZ_CCW_N)
              );
              /* Start the az-el wave */
              e = gpioWaveTxSend(azel_wave, PI_WAVE_MODE_REPEAT);
              if(e < 0)
              {
                fprintf(stderr, "Failed to send Az drive waveform: %d\n", e);
              }
              pwm_state = WAVE_AZEL;
            }
            else
            {
              /* Start the az-only wave */
              e = gpioWaveTxSend(az_wave, PI_WAVE_MODE_REPEAT);
              if(e < 0)
              {
                fprintf(stderr, "Failed to send Az drive waveform: %d\n", e);
              }
              pwm_state = WAVE_AZ;
            }
          }
        }
      }
      else if(app_state->error_az_deg < (-1 * AZ_HYSTERESIS)
        && (az_relay_lastswitch + AZ_RELAY_PAUSE_MS) < timestamp_ms())
      {
        if(az_relay_state == 1)
        {
          gpioWrite(AZ_SWITCH_GPIO, 0);
          az_relay_state = 0;
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

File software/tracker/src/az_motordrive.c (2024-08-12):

#include <stdio.h>
#include <stdlib.h>
#include <unistd.h>
#include <stdbool.h>
#include <signal.h>

#include <math.h>
#include <pigpio.h>

#include "main.h"

#define WAVEFORM_POINTS     (1000)
#define WAVEFORM_PERIOD_US  (40)

#define AZ_CW_P     (24)
#define AZ_CW_N     (25)

#define AZ_CCW_P    (5) // unused (popped)
#define AZ_CCW_N    (6) // unused (popped)

#define AZ_SWITCH_GPIO  (27)

void *az_motordrive_thread(void *arg)
{
  app_state_t *app_state = (app_state_t *)arg;


  float phase_angle, sine_amplitude, duty_cycle;
  int gpio;

  /* Clear Waves */
  int e __attribute__((unused));

  gpioPulse_t *dir_a_wf = (gpioPulse_t *)malloc(WAVEFORM_POINTS * sizeof(gpioPulse_t));
  if(dir_a_wf == NULL)
  {
    fprintf(stderr, "Error allocating local memory for waveform\n");
    return NULL;
  }

  for(int i = 0; i < WAVEFORM_POINTS; i++)
  {
    phase_angle = i * ((2*M_PI) / (float)WAVEFORM_POINTS);
    sine_amplitude = sin(phase_angle);

    if(sine_amplitude >= 0)
    {
      /* Positive half of wave */
      gpio = 1 << (AZ_CW_P);
    }
    else
    {
      gpio = 1 << (AZ_CW_N);
    }

    duty_cycle = fabs(sine_amplitude) * 0.9;

    if((i & 0x01) == 0x00)
    {
      dir_a_wf[i].gpioOn = gpio;
      dir_a_wf[i].gpioOff = 0;
      dir_a_wf[i].usDelay = (int)(round(duty_cycle * WAVEFORM_PERIOD_US));
      //printf("%06d (%f dc)\n", dir_a_wf[i].usDelay, duty_cycle);
    }
    else
    {
      dir_a_wf[i].gpioOn = 0;
      dir_a_wf[i].gpioOff = gpio;
      dir_a_wf[i].usDelay = WAVEFORM_PERIOD_US - (int)(round(duty_cycle * WAVEFORM_PERIOD_US));
    }
  }

  e = gpioWaveAddGeneric(WAVEFORM_POINTS, dir_a_wf);
  if(e < 0)
  {
    fprintf(stderr, "Failed to add Az Waveform to gpio: %d\n", e);
  }
  //int dir_a_points = gpioWaveAddGeneric(WAVEFORM_POINTS, dir_a_wf);
  //printf("Dir A Pulses: %d\n", dir_a_points);

  int dir_a_wave __attribute__((unused)) = gpioWaveCreate();
  if(dir_a_wave < 0)
  {
    fprintf(stderr, "Failed to create Az Waveform: %d\n", e);
  }

  /* Set up outputs */

  gpioSetMode(AZ_CW_P, PI_OUTPUT);
  gpioSetMode(AZ_CW_N, PI_OUTPUT);

  gpioSetMode(AZ_CCW_P, PI_OUTPUT);
  gpioSetMode(AZ_CCW_N, PI_OUTPUT);

  gpioWrite_Bits_0_31_Clear(
    1 << (AZ_CW_P) | 1 << (AZ_CW_N) | 1 << (AZ_CCW_P) | 1 << (AZ_CCW_N)
  );

  /* Direction Relays */
  gpioSetMode(AZ_SWITCH_GPIO, PI_OUTPUT);

  gpioWrite(AZ_SWITCH_GPIO, 0);

  int32_t relay_state = 0;
  int32_t pwm_state = 0;

  /* Run waves */
  while(!(app_state->app_exit))
  {
    if(app_state->demand_valid
      && app_state->current_valid
    )
    {
      if(app_state->demand_az_deg < (app_state->current_az_deg - 1.5)) // 0.5 hysteresis
      {
        if(relay_state == 0)
        {
          gpioWrite(AZ_SWITCH_GPIO, 1);
          relay_state = 1;

          usleep(300*1000);
        }
        if(pwm_state == 0)
        {
          e = gpioWaveTxSend(dir_a_wave, PI_WAVE_MODE_REPEAT);
          pwm_state = 1;
        }
      }
      else if(app_state->demand_az_deg > (app_state->current_az_deg + 1.5)) // 0.5 hysteresis
      {
        if(relay_state == 1)
        {
          gpioWrite(AZ_SWITCH_GPIO, 0);
          relay_state = 0;

          usleep(300*1000);
        }

        if(pwm_state == 0)
        {
          printf("driving cw..");
          e = gpioWaveTxSend(dir_a_wave, PI_WAVE_MODE_REPEAT);
          if(e < 0)
          {
            fprintf(stderr, "Failed to send Az drive waveform: %d\n", e);
          }
          pwm_state = 1;
        }
      }
      else
      {
        /* Can stop */

        if(pwm_state == 1)
        {
          gpioWaveTxStop();
          gpioWrite_Bits_0_31_Clear(
            1 << (AZ_CW_P) | 1 << (AZ_CW_N) | 1 << (AZ_CCW_P) | 1 << (AZ_CCW_N)
          );

          pwm_state = 0;
        }
      }
    }
    else
    {
      /* Not valid */

      if(pwm_state == 1)
      {
        gpioWaveTxStop();
        gpioWrite_Bits_0_31_Clear(
          1 << (AZ_CW_P) | 1 << (AZ_CW_N) | 1 << (AZ_CCW_P) | 1 << (AZ_CCW_N)
        );

        pwm_state = 0;
      }
    }

    usleep(100*1000);
  }

  printf("Az motordrive thread exiting..\n");

  gpioWaveTxStop();

  gpioWrite_Bits_0_31_Clear(
      1 << (AZ_CW_P) | 1 << (AZ_CW_N) | 1 << (AZ_CCW_P) | 1 << (AZ_CCW_N)
    );

  gpioWrite(AZ_SWITCH_GPIO, 0);

  return NULL;
}
